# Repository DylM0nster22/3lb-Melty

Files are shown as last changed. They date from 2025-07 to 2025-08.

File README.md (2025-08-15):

# Unschuled dissasembly a 3lb "meltybrain" combat robot

This is a 3lb combat robot that me and luke have designed. this is a special type of robot thats way more complcated then normal bots, normal bots just have normal wheels and then the spinning weapon right well this bot is the weapon, the two hugely overpowered motors act as drive motors set to spin oppisite directions from eachother so the enitre 3lb mass of the robot is the weapon for a greater moi and impact. this can be achieved by using a microcontroller like a arduino nano or in my case a adafruint itsybitsy 32u4 and hooking it to the reciever and allowing it to act as a controller for the motor escs instead of the reciever and what is then does is edit the pwn that the escs get to allow translational drift to happen which is when even when the entire robot is spinning at 5000 rpm it can still go in a mostly stright line. 

# About this project 
This project includes a custom pcb for all the wiring of motors, escs, adafruit and the accelerometer. the pcb also acts as a power distrubution board which i struggled with for a while because of the amount of power going throught it, the back pads of the escs are going to be filled with solder to help conduct the electricity better and allow for more heat disspation. all the vias are also going to be filled to the brim with solder. i also created a reverse polarity protection circuit for the electronics other then the escs using a mosfet. the weapons are going to be made out of ar500 steel for the strength to weight ratio. the pcb is going to cost extra because it has to be 2oz copper, this was a fun and painful project to learn how to make pcbs on. i know buying spares of parts is frowned opon but its the same price without the spare weapon, i also left the carbon fibre out of the bom because theres not enough time to get it quoted.



471334013-767f2554-9c21-4e59-9d07-b84de258acd2



| Parts | Amount | Cost | Total Cost | Weight | Total Weight | Provider | |
|---|---|---|---|---|---|---|---|
| | | | | | | | |
| Drive/Weapon motor | 2 | $34.59 | $69.18 | 156 | 312 | [HobbyKing](https://hobbyking.com/en_us/propdrive-v2-3542a-1250kv-brushless-outrunner-motor.html) | PROPDRIVE v2 3542 1250KV Brushless Outrunner Motor |
| ESC | 2 | $30.00 | $60.00 | 13.9 | 27.8 | [Amazon](https://a.co/d/5kXJAQ6) | HGLRC Specter 90A 8S BLheli32 Single ESC |
| Battery | 1 | $62.99 | $62.99 | 370 | 370 | [Amazon](https://www.amazon.com/OVONIC-Battery-3500mAh-14-8V-Connector/dp/B0DF1V1Z6P/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) | OVONIC 4S LiPo Battery 3500mAh 14.8V 130C |
| Reciever | 1 | $5.67  | $5.67 | 0.9 | 0.9 | [Aliexpress](https://www.aliexpress.us/item/3256804714662317.html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) | FS2A 4CH AFHDS 2A |
| Power switch | 1 | $12.50 | $12.50 | 3 | 3 | [Repeat Robotics](https://repeat-robotics.com/buy/lynx-robot-switch/) | Lynx Anti-Spark Switch |
| xt90 connector | 1 | $12.99 | $12.99 | 18 | 36 | [Amazon](https://www.amazon.com/Yaohappy-Female-Bullet-Connectors-Battery/dp/B09L7GVWQ3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) | xt90 connector |
| Buck Converter | 1 | $3.55  | $3.55 | 3.85 | 3.85 | [Amazon](https://www.amazon.com/MEIVIFPV-Adjustable-Step-Down-Regulator-Quadcopter/dp/B0FCXTHX6W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) | Micro voltage regulator |
| N-Channel mosfet | 1 | $2.23 | $2.23 | negligible | negligible | [Aliexpress](https://www.aliexpress.us/item/3256805136051666.html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) | N-Channel Enhancement-Mode MOSFET Transistor 60V 115mA,SOT-23. |
| Accelerometer | 1 | $25 | $25 | Unknown | Unknown | [Adafruit](https://www.adafruit.com/product/4627#technical-details) | Adafruit H3LIS331 Ultra High Range Triple-Axis Accelerometer |
| Pin headers | 1 | $1.68  | $1.68 | negligible | negligible | [Aliexpress](https://www.aliexpress.us/item/2255800801798474.html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) | 40 pin Breakable Pin Header |
| P-Channel mosfet | 1 | $2.83  | $2.83 | negligible | negligible | [Aliexpress](https://www.aliexpress.us/item/3256807719253034.html?productId=3256807719253034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) | SUM110P06-07L-E3 p channel mosfet |
| Blue LED | 1 | $ 3.68 | $3.68 | 2.8 | 2.8 | [Aliexpress](https://www.aliexpress.us/item/3256803137393104.html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) | Clear blue LED Diode Lights |
| Zener Diode | 1 | $2.02  | $2.02 | negligible | negligible | [Aliexpress](https://www.aliexpress.us/item/3256807042309359.html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) | 15v zener diode |
| Resistor set | 1 | $2.18 | $2.18 | negligible | negligible | [Aliexpress](https://www.aliexpress.us/item/3256807449715737.html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) | 0805 Chip Resistor Assortment Kit |
| Ceramic Capacitor 47uf | 1 | $2.62  | $2.62 | negligible | negligible | [Aliexpress](https://www.aliexpress.us/item/3256805862294240.html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) | 0805 47UF 25V X7R M |
| Electrolytic Capacitor | 1 | $3.64 | $3.64 | 33 | 33 | [Aliexpress](https://www.aliexpress.us/item/3256802246707783.html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) | 4700uF 35V 18x30mm Electrolytic Capacitor |
| 0.1UF Caps | 1 | $2.6 | $2.6 | negligible | negligible | [Aliexpress](https://www.aliexpress.us/item/3256806974673655.html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) | |
| ATMEGA32U4-AU | 2 | $4.11  | 8.22 | negligible | negligible | [Aliexpress](https://www.aliexpress.us/item/3256808047819136.html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) | |
| 22PF Caps | 1 | $2.6 | $2.6 | negligible | negligible | [Aliexpress](https://www.aliexpress.us/item/3256806974673655.html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) | |
| Ceramic Capacitor 10UF | 1 | $2.62  | $2.62 | negligible | negligible | [Aliexpress](https://www.aliexpress.us/item/3256805862294240.html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) | 0805 47UF 25V X7R M) |
| 10NF Caps | 1 | $2.6 | $2.6 | negligible | negligible | [Aliexpress](https://www.aliexpress.us/item/3256806974673655.html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) | |
| USB-C-PORT | 1 | $1.43  | 1.43 | negligible | negligible | [Aliexpress](https://www.aliexpress.us/item/3256808618842348.html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) | |
| USBLC6-4SC6 | 1 | $0.84  | $0.84 | negligible | negligible | [Aliexpress](https://www.aliexpress.us/item/3256807215523812.html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) | |
| Weapon | 3 | $10 | $31 | | | [SendCutSend]( | ar500 steel weapon |
| PCB | 1 | $27.50 | $27.50 | | | [JLCPCB]( | pcb for power distrubution and connections to mcu and escs |
| | | | | | | | |
| Body | 1 | $0.00  | $0.00 | | | | |
| | | | $352.17 | | 1175.95 | | |

source for code https://github.com/nothinglabs/openmelt2

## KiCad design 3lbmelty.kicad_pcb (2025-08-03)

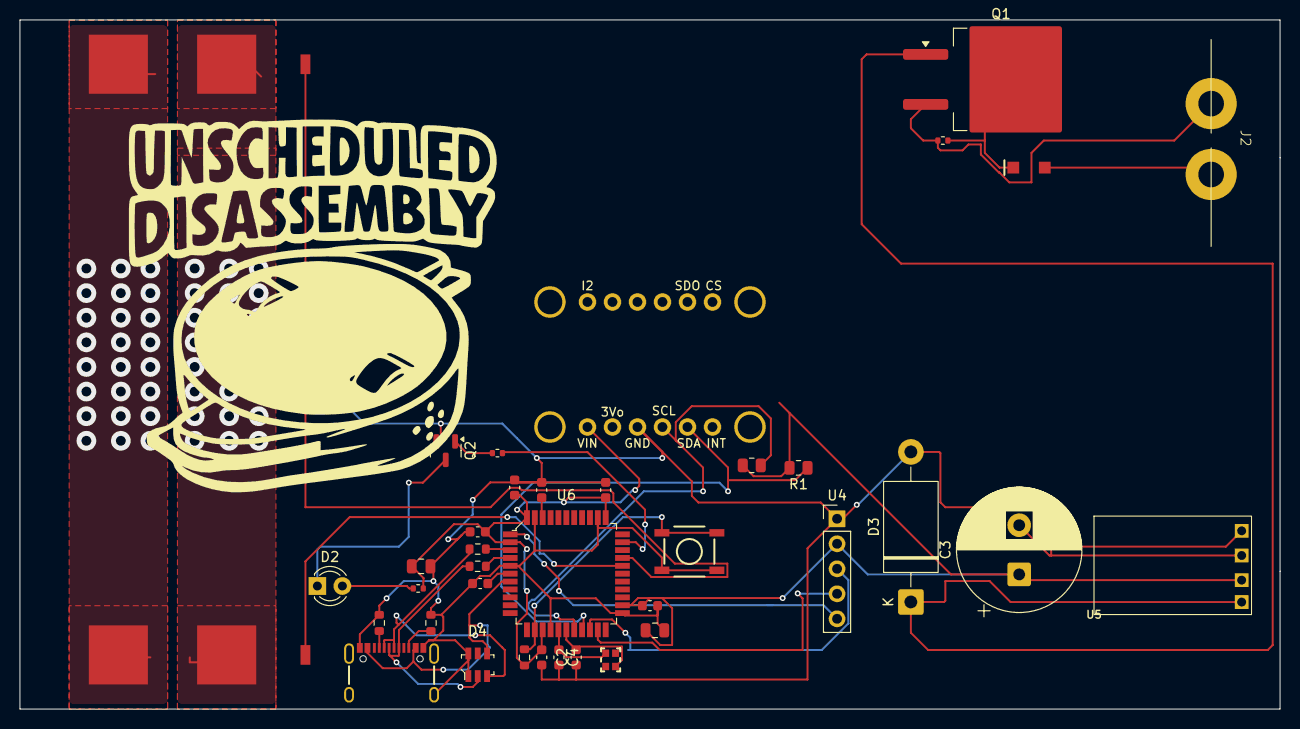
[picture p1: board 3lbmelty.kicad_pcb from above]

Board: 2 copper layers, 128.0 x 70.0 mm, 38 parts (0 on the bottom side), 28 nets.

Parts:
C1: 47uF; C_0805_2012Metric
C1#2, C5, C6, C7, C8, C9: 0.1uF; C_0603_1608Metric
C2, C4: 22pF; C_0603_1608Metric
C3: 4700uF; CP_Radial_D12.5mm_P5.00mm
C11: 10uF; C_0805_2012Metric
C12: 10nF; C_0603_1608Metric
D1: D_Zener; SOD-123
D2: Blue LED ~ 3.5v / 20ma; LED_D3.0mm
D3: 1.5KExxA; D_DO-201AE_P15.24mm_Horizontal
D4: USBLC6-4SC6; SOT23-6L
J1: Esc 2; ESC
J2: Amass_XT90-S; Amass_XT60PW
J3: Esc 1; ESC
J4: USB_C_Receptacle; USB-C_16
Q1: SUM110P06-07L-E3; TO-263-2
Q2: 2N7002; SOT-23
R1, R2: 4.7k; R_0805_2012Metric
R3: 10k; R_0402_1005Metric
R4: 1k; R_0402_1005Metric
R5: 150; R_0402_1005Metric
R6, R7: 22; R_0603_1608Metric
R8: 10k; R_0603_1608Metric
R9, R10: 5.1k; R_0603_1608Metric
SW1: SMD_5.2x5.2mm_h1.5mm; Push_SMD_5.2x5.2mm_h1.9mm
U2: Adafruit_H3LIS311_Breakout; h3
U4: RC_RECEIVER; PinHeader_1x05_P2.54mm_Vertical
U5: BUCK_CONVERTER; MP1584
U6: ATMEGA32U4-AU; TQFP-44_10x10mm
Y1: 16MHz; Crystal_SMD_2.0x1.6mm

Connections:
5v: C1.1, C3.1, C5.2, C6.1, C7.1, C8.1, C9.1, C11.1, R1.2, R2.2, R5.1, R8.1, U2.1 (VIN), U4.2 (+V), U5.OUT+, U6.2 (UVCC), U6.14 (VCC), U6.24 (AVCC), U6.34 (VCC), U6.44 (AVCC)
BAT: J1.1, J2.1, J3.1, Q1.3 (S), R3.2
BAT_SAFE: D3.1 (A1), Q1.1 (D), U5.IN+
D+: D4.2, J4.A6 (D+), J4.B6 (D+), R6.1
D-: D4.3, J4.A7 (D-), J4.B7 (D-), R7.1
GND: C1.2, C1#2.1, C2.1, C3.2, C4.2, C5.1, C6.2, C7.2, C8.2, C9.2, C11.2, C12.2, D1.2 (A), D3.2 (A2), D4.1, D4.6, J1.3, J2.2, J3.3, J4.GND, J4.S (SHIELD), Q2.2 (S), R9.2, R10.1, SW1.2, U2.3 (GND), U4.1 (GND), U5.IN-, U5.OUT-, U6.5 (UGND), U6.15 (GND), U6.23 (GND), U6.35 (GND), U6.43 (GND)
MOTOR_1: J3.2, U6.29 (PB5)
MOTOR_2: J1.2, U6.30 (PB6)
unnamed: D1.1 (K), Q1.2 (G), R3.1
unnamed: D2.2 (A), R5.2
unnamed: D2.1 (K), Q2.3 (D)
unnamed: J4.A5 (CC1), R9.1
unnamed: J4.B5 (CC2), R10.2
unnamed: Q2.1 (G), R4.2
unnamed: C1#2.2, U6.42 (AREF)
unnamed: R6.2, U6.4 (D+)
unnamed: R7.2, U6.3 (D-)
unnamed: R4.1, U6.32 (PC7)
unnamed: C12.1, U6.6 (UCAP)
unnamed: C2.2, U6.17 (XTAL1), Y1.1
unnamed: C4.1, U6.16 (XTAL2), Y1.2
RC1: U4.5 (CH1), U6.1 (PE6)
RC2: U4.4 (CH2), U6.21 (PD3)
RC3: U4.3 (CH3), U6.20 (PD2)
Reset: R8.2, SW1.1, U6.13 (~RES)
SCL: R2.1, U2.4 (SCL), U6.18 (PD0)
SDA: R1.1, U2.5 (SDA), U6.19 (PD1)
VBUS: D4.4, J4.VBUS, U6.7 (VBUS)

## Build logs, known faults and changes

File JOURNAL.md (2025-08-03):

---
title: "3lb MeltyBrain"
author: "Dylan and Luke"
description: "This is going to be a 3lb meltybrain that has a custom pcb to control pwm movement and distrubte power"
created_at: "2025-28-6"
---
# Total Time Spent 43hr

# June 28th: Researching parts, weight, and costs

Today is the start of the next bot, today will mainly consist of making a basic BOM, researching how to connect everything, and how to start designing the pcb for it. We also decided on the name of the bot... unscheduled dissasembly. Dylan worked on making the BOM and looked into what would need to be done to make the pcb. Luke sat on call with dylan and helped out with the BOM. After being on call for one hour we came up with the tenative BOM.



With this BOM we have two 3536 drone motors as our main drive motors and two 90a esc's that Dylan found a good deal on. We also decieded on running the bot on a 3500 mah 4s battery, on lukes suggestion we are going to run carbon fiber for top and bottom plates with ar500 or s7 tool steel teeth somehow screws into a tpu body. 

**Total Time Spent 1.5hr**

# June 29th: making the cad and trying to make the pcb

Today luke designed the enitre meltybrain robot while on a call with dylan. Dylan started trying to make the pcb and tried different ideas and custom things but completly failed at all of them. Luke spent around 8hr making the meltybrain cad and its mostly done, dylan had no progress to speak of other than deciding on a plan.





**Total time spent 8hr**

# July 18th: Starting the PCB

Today Dylan started the design of the pcb and got pretty close to finishing the schematic, he added the mcu which is a xiao esp32 breakout board, the mcu an h3lis311 breakout board, the reciever which is a fs-2a, the led, the xt60, and he still needs to add things like voltage regulator pads and other various things. tommorow will most likely consist of mainly wiring the pcb.



**Total time spent 6hr**

# July 20th: Getting closer to wiring the PCB

Dylan didnt have time to work on the PCB yesterday and today he learned he wasnt even close to done with the schematic, the mcu that was being used was the wrong type so that was switched to an Adafruit ItsyBitsy 32u4 - 5V 16MHz because its the correct architecture for the opensource code were using/editing called openmelt2. He also learned that a xt60 wasnt nearly big enough for this so the bot is now going to use a xt90 which supports up to 90a. tommorow will consist of adding resistors, diodes, cap's, etc, then maybe after all that wiring the PCB. oh and a buck converter was also added to keep everything at 5v. Most of the time was spent remakeing things and relizing nothing works.



**Total time spent 5hr**

# July 21st: added the rest of things to schematic

Today dylan worked on the schematic and added things like caps, resistors, mosfets, and diodes, he also added everything that is needed into the bom, the price might be over 350$ so luke might need to split the extra. the big main mosfet is for in case the power gets applied backwards all the electronics dont die, the diode is to help reduce noise.



**Total time spent 3hr**

# July 22nd: starting the pcb part

Today dylan spent too long to count looking for footprints before relizing that he has to make some of them himself or find ones close enough then edit them, he placed most of the components in a way that might work but might have to change it later, he also made the boundey of 48x128mm which is how big the current comparment of the bot is. 



**Total time spent 4hr**

# July 23rd: Continuing on the PCB

Today Dylan finally started getting into the grove of how kicad works after spending too many hours on it, he also learned that 90a on 16.4v is alot of power and needs thick traces, about 10mm with 2oz copper and solder all over those 10mm lines so that fun. he also relized that the current boundries were too small for both the normal bot componenets and the pcb so the pcb is now 28 mm longer yay more room. he had fights with the mcu footprint and the accelarometer footprint for a while because neither of them were working correctly with pins and whatnot until he changed the pins in the footprint which took him hours to learn. overall most of the placement is decided, this bot is going to be spinning stupid fast around 300mph, for the acceloreter to not be oversatured it needs to be exactly in the ceneter, even 10mm out from the center could reach almost 5000 g's. there is too much open space in the pcb perfect for some art.



**Total time spent 3hr**

# July 27th: Finishing the PCB and editing the CAD

Today luke didnt exist so dylan did everything, the start of today was routing the pcb and figureing out how to make those big traces i was talking about, routing took a bit because i had to remember how to flip wires on the underside of the board and figure out how to make the big traces. i learned instead of normal traces what i needed was zones of copper, and to make it so everything was easier to route i make those zones on the bottom of the board. during the routing process i relized that where i had the pins for the reciever to the mcu set wrong so i had to change that. on the Cad side of things i had to make the space changes i talked about earlier to make the pcb fit and i also learned luke wasnt as done with the cad as i though. I added things like more support for the center of the bot, mounting holes for the weapons, wheels and rims, making the whole things 6mm taller, adding the escs, and adding screw holes to the bottom plate. tommorow i will need to make a way to mount the tires to the rims and add screw holes to the top lid and do some final weight calculations and hope that im not somehow out of weight, oh and i also learned that i am overbudget by a good amount so thats fun. while i was typing this big paragraph i was letting fusion render the cad so thats nice.







**Total time spent 8hr**

# July 28th: spent some time on finishing touches and weight calculations

Today didnt consist of much just some small things like adding screw holes to the top. send cut send is really fun with pricing see the images below which is why theres three weapons instead of just two. i think this is the end of it, time to submit and hope for the best. there is carbon fibre needed but were going to buy it separately.





**Total time spend 45 min**

# August 2nd: working on the pcb to make it better 

So our project didnt get approved for 10 points because the pcb was essentially a plug in external modules, but now it has a fully custom wires mcu which is a atmega32u4, i did everything like the decoupleing caps and the reset buttons and eveyrthing so hopefully ill be able to get approved for 10 points now, i spend the first 30 ish minutes researching the mcu and what pins did what and stuff, then i imported it and all the other things. i decieded on using usb-c because its the more used port out of what i have so that brought its own challenges. by far the hardest part was getting all the wires to everything because with the smaller chip and all the added things there was like no room left so there are alot of vias, i also relized i had to move the resistors as i was wiring this because two were under the accelormeter which wouldent work well.





Edit found a issue with power and resolved it rq 



**Total time spent 4.25hr**

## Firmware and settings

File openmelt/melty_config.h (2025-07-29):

//This file is intended to include all commonly modified settings for Open Melt

#ifndef MELTY_CONFIG_GUARD  //header guard
#define MELTY_CONFIG_GUARD

//----------AVR SPECIFIC FUNCTIONALITY----------
//This code has not been tested on ARM / non-AVR Arduinos (but may work)
//Doesn't currently support persistent config storage for non-AVR Arduinos (see config_storage.cpp for details)
//490Hz PWM-throttle behavior is specific to Atmega32u4 (see below)

//----------DIAGNOSTICS----------
//#define JUST_DO_DIAGNOSTIC_LOOP                 //Disables the robot / just displays config / battery voltage / RC info via serial

//----------EEPROM----------
#define ENABLE_EEPROM_STORAGE                     //Comment out this to disable EEPROM (for ARM)
#define EEPROM_WRITTEN_SENTINEL_VALUE 42          //Changing this value will cause existing EEPROM values to be invalidated (revert to defaults)

//----------TRANSLATIONAL DRIFT SETTINGS----------
//"DEFAULT" values are overriden by interactive config / stored in EEPROM (interactive config will be easier if they are about correct)
//To force these values to take effect after interactive config - increment EEPROM_WRITTEN_SENTINEL_VALUE
#define DEFAULT_ACCEL_MOUNT_RADIUS_CM 3.9         //Radius of accelerometer from center of robot
#define DEFAULT_LED_OFFSET_PERCENT 7              //Adjust to make heading LED line up with direction robot travels 0-99 (increasing moves beacon clockwise)
                                                   
#define DEFAULT_ACCEL_ZERO_G_OFFSET 0.0f          //Value accelerometer returns with robot at rest (in G) - adjusts for any offset
                                                  //H3LIS331 claims +/-1g DC offset - typical - but +/-2.5 has been observed at +/-400g setting (enough to cause tracking error)
                                                  //Just enterring and exiting config mode will automatically set this value / save to EEPROM (based on current accel reading reflecting 0g)
                                                  //For small-radius bots - try changing to H3LIS331 to +/-200g range for improved accuracy (accel_handler.h)

#define LEFT_RIGHT_HEADING_CONTROL_DIVISOR 1.5f   //How quick steering is (larger values = slower)

#define MIN_TRANSLATION_RPM 400                   //full power spin in below this number (increasing can reduce spin-up time)


//----------PIN MAPPINGS----------
//RC pins must be Arduino interrupt pins
//we need 3 interrupt pins - which requires an Arduino with Atmega32u4 or better (Atmega328 only support 2 interrupts)
//Common RC receiver setup LEFTRIGHT = CH1, FORBACK = CH2, THROTTLE = CH3
//Note: Accelerometer is connected with default Arduino SDA / SCL pins

#define LEFTRIGHT_RC_CHANNEL_PIN 7                //To Left / Right on RC receiver
#define FORBACK_RC_CHANNEL_PIN 1                  //To Forward / Back on RC receiver (Pin 1 on Arduino Micro labelled as "TX" - https://docs.arduino.cc/hacking/hardware/PinMapping32u4)
#define THROTTLE_RC_CHANNEL_PIN 0                 //To Throttle on RC receiver (Pin 0 on Arduino Micro labelled as "RX" - https://docs.arduino.cc/hacking/hardware/PinMapping32u4)

#define HEADING_LED_PIN	13                         //To heading LED (pin 13 is on-board Arduino LED)

//no configuration changes are needed if only 1 motor is used!
#define MOTOR_PIN1 9                              //Pin for Motor 1 driver
#define MOTOR_PIN2 10                             //Pin for Motor 2 driver

#define BATTERY_ADC_PIN A0                        //Pin for battery monitor (if enabled)


//----------THROTTLE CONFIGURATION----------
//THROTTLE_TYPE / High-speed PWM motor driver support:
//Setting THROTTLE_TYPE to FIXED_PWM_THROTTLE or DYNAMIC_PWM_THROTTLE pulses 490Hz PWM signal on motor drive pins at specified duty cycle (0-255)
//Can be used for 2 possible purposes:
//  1. Used as control signal for a brushless ESC supporting high speed (490Hz) PWM (tested with Hobbypower 30A / "Simonk" firmware)
//          Assumes Arduino PWM output is 490Hz (such as Arduino Micro pins 9 and 10) - should be expected NOT to work with non-AVR Arduino's without changes
//  2. 490hz signal maybe fed into a MOSFET or other on / off motor driver to control drive strength (relatively low frequency)
//Thanks to Richard Wong for his research in implementing brushless ESC support

enum throttle_modes {
  BINARY_THROTTLE,      //Motors pins are fully on/off - throttle controlled by portion of each rotation motor is on (no PWM)

  FIXED_PWM_THROTTLE,   //Motors pins are PWM at PWM_MOTOR_ON, PWM_MOTOR_COAST or PWM_MOTOR_OFF
                        //throttle controlled by portion of each rotation motor is on

  DYNAMIC_PWM_THROTTLE  //Scales PWM throttling between PWM_MOTOR_COAST and PWM_MOTOR_ON
                        //Range of throttle scaled over is determined by DYNAMIC_PWM_THROTTLE_PERCENT_MAX
                        //PWM is locked at PWM_MOTOR_ON for throttle positions higher than DYNAMIC_PWM_THROTTLE_PERCENT_MAX
                        //Robot speed is additionally controlled by portion of each rotation motor is on (unless DYNAMIC_PWM_MOTOR_ON_PORTION is defined)
                        //This mode reduces current levels during spin up at part throttle
};

#define THROTTLE_TYPE DYNAMIC_PWM_THROTTLE    //<---Throttle type set here!

#define DYNAMIC_PWM_MOTOR_ON_PORTION 0.5f       //if defined (and DYNAMIC_PWM_THROTTLE is set) portion of each rotation motor is on is fixed at this value
                                                //About 0.5f for best translation (higher for increased RPM)

#define DYNAMIC_PWM_THROTTLE_PERCENT_MAX 1.0f   //Range of RC throttle DYNAMIC_PWM_THROTTLE is applied to 
                                                //0.5f for 0-50% throttle (full PWM_MOTOR_ON used for >50% throttle)
                                                //1.0f for 0-100% throttle

//----------PWM MOTOR SETTINGS---------- 
//(only used if a PWM throttle mode is chosen)
//PWM values are 0-255 duty cycle
#define PWM_MOTOR_ON 230                          //Motor PWM ON duty cycle (Simonk: 140 seems barely on / 230 seems a good near-full-throttle value)
#define PWM_MOTOR_COAST 100                       //Motor PWM COAST duty cycle - set to same as PWM_ESC_MOTOR_OFF for fully unpowered (best translation?)
#define PWM_MOTOR_OFF 100                         //Motor PWM OFF duty cycle (Simonk: 100 worked well in testing - if this is too low - ESC may not init)


//----------BATTERY MONITOR----------
#define BATTERY_ALERT_ENABLED                     //if enabled - heading LED will flicker when battery voltage is low
#define VOLTAGE_DIVIDER 11                        //(~10:1 works well - 10kohm to GND, 100kohm to Bat+).  Resistors have tolerances!  Adjust as needed...
#define BATTERY_ADC_WARN_VOLTAGE_THRESHOLD 7.0f  //If voltage drops below this value - then alert is triggered
#define ARDUINIO_VOLTAGE 5.0f                     //Needed for ADC maths for battery monitor
#define LOW_BAT_REPEAT_READS_BEFORE_ALARM 20      //Requires this many ADC reads below threshold before alarming


//----------SAFETY----------
#define ENABLE_WATCHDOG                           //Uses Adafruit's sleepdog to enable watchdog / reset (tested on AVR - should work for ARM https://github.com/adafruit/Adafruit_SleepyDog)
#define WATCH_DOG_TIMEOUT_MS 2000                 //Timeout value for watchdog (not all values are supported - 2000ms verified with Arudino Micro)
#define VERIFY_RC_THROTTLE_ZERO_AT_BOOT           //Requires RC throttle be 0% at boot to allow spin-up for duration of MAX_MS_BETWEEN_RC_UPDATES (about 1 second)
                                                  //Intended as safety feature to prevent bot from spinning up at power-on if RC was inadvertently left on.
                                                  //Downside is if unexpected reboot occurs during a fight - driver will need to set throttle to zero before power 

#endif

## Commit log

2025-07-29 Update and rename 3lb Meltybrain - Sheet1.csv to BOM.csv
    [BOM.csv]
2025-07-30 added pcb files
    [3lbmelty.kicad_pcb, 3lbmelty.kicad_sch]
2025-08-03 new pcb
    [3lbmelty.kicad_pcb, 3lbmelty.kicad_sch]
2025-08-03 fixed small issue with resistor placement
    [3lbmelty.kicad_pcb]
